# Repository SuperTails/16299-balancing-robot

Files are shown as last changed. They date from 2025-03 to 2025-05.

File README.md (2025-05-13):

# 16299 Balancing Robot PCB

Updated version of the PCB for 16299.

A submodule is used for some parts, so be sure to clone recursively:
```bash
git clone --recursive https://github.com/SuperTails/16299-balancing-robot.git
```

## Ordering PCBs

### 1 - Generate Bill of Materials

To generate the BoM:

1. Open the schematic editor
2. Open the "edit symbol fields" menu (table icon along the top ribbon)
3. Ensure the settings are as shown below
4. Hit "export".

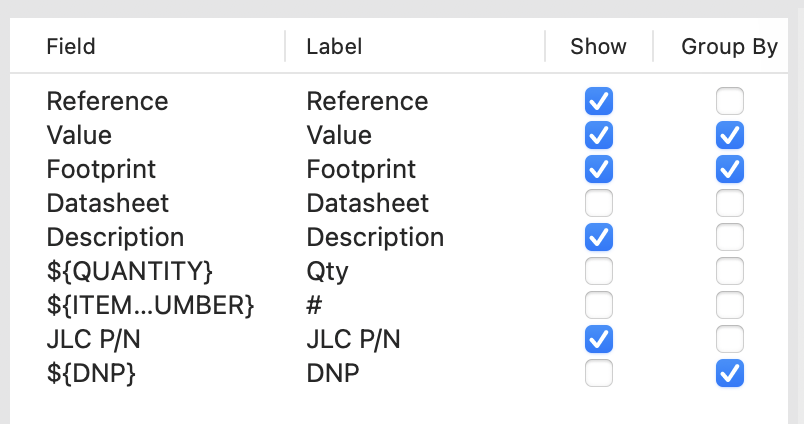
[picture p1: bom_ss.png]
BOM settings


### 2 - Generate Gerber Files

To generate the gerber files:
1. Open the PCB editor
2. File > Fabrication Outputs > Gerbers (.gbr)...
3. Ensure the settings are as shown below, including...
4. ... Make sure you set your output folder to `fab/`.
5. Click "Plot"

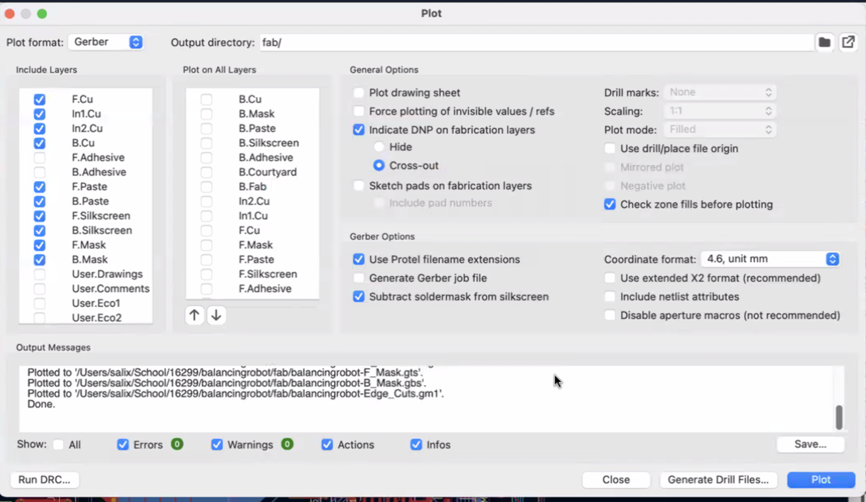
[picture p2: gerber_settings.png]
Gerber settings


More information for plotting Gerber and Drill files is available on
[JLC's guide](https://jlcpcb.com/help/article/how-to-generate-gerber-and-drill-files-in-kicad-7).

### 3 - Generate Drill Files

To generate the drill files:
1. From the Gerbers menu in the previous step, click "Generate Drill Files"
3. Ensure the settings are as shown below
5. Click "Generate"

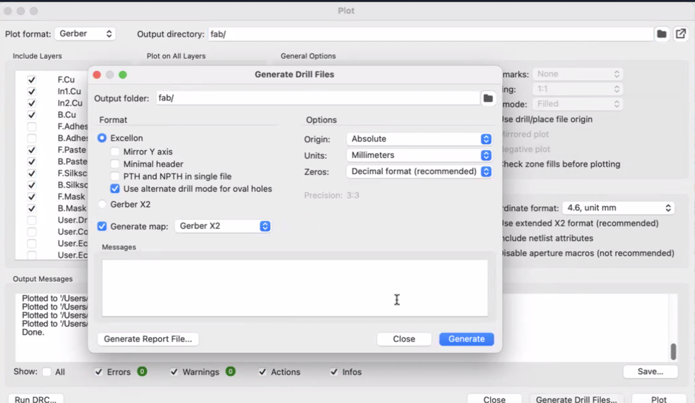
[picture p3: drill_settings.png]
Drill settings


More information for plotting Gerber and Drill files is available on
[JLC's guide](https://jlcpcb.com/help/article/how-to-generate-gerber-and-drill-files-in-kicad-7).

### 4 - Generate Placement Files

To generate the placement files:
1. Open the PCB editor
2. File > Fabrication Outputs > Component Placement (.pos, .gbr)...
3. Ensure the settings are as shown below
4. Click "Generate Position File"

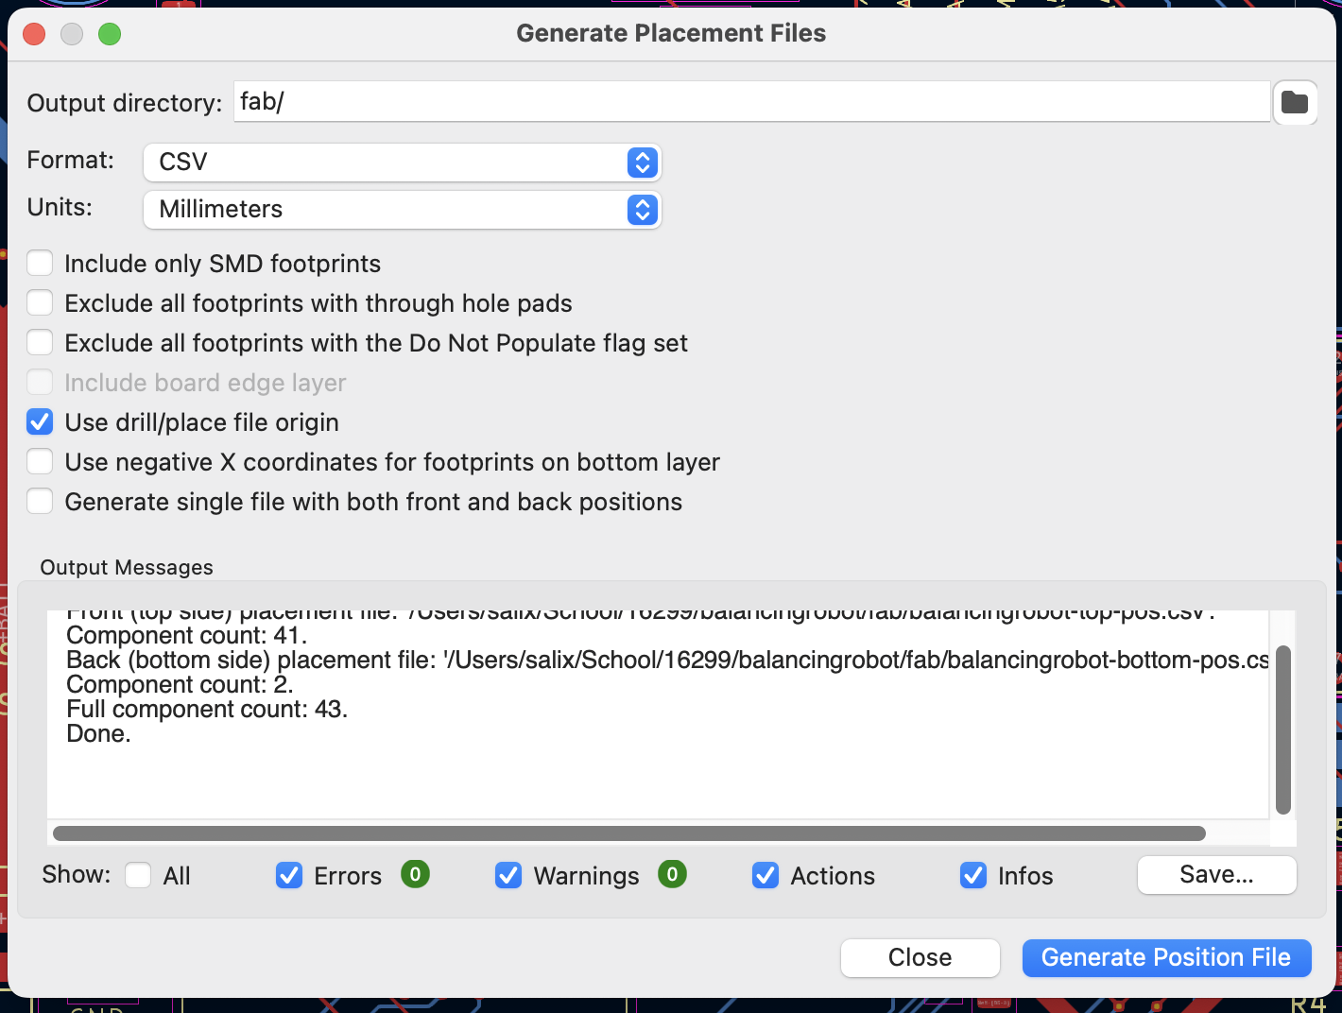
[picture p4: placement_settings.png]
Placement settings


### 5 - File Format Conversion

To convert the files into JLC's preferred format, run the `format_bom.py` script:

```bash
python3 format_bom.py
```

This will generate `fab/bom-jlc.csv` and `fab/balancingrobot-top-pos-jlc.csv`,
which should be used for JLC's PCB assembly options (discussed later).

### 6 - Upload Gerbers

Zip the `fab/` directory and upload it to [JLC's website](https://jlcpcb.com/).
Rarely, the file upload can take up to 10 minutes to complete.

### 7 - Select Ordering Options

Most settings should default correctly,
but there are a few changes:

1. Set the quantity to the desired amount
2. Ensure that the order mark is set to "Order Number (Specify Position)"
3. Enable "PCB Assembly"
4. Hit "next"

Quantity settings
Order settings
PCBA settings

### 8 - Uploading BOM and Placing Components

When prompted to "Upload BOM" and "Add CPL file",
upload `fab/bom-jlc.csv` and `fab/balancingrobot-top-pos-jlc.csv`.

It may issue a warning that D9 and D10 are not present in the CPL,
this is normal and you can continue.
D9 and D10 are the IR LEDs which are mounted on the underside of the board,
and doing assembly for both top and bottom components makes shipping difficult.

All parts should be selected in the right column and there should be no other errors.

When moving on to placement, JLC may note that
"The system detects component that may be offset from the PCB,
does it try to automatically align it?"
Click **cancel** on this prompt, as it will displace many of the components to the wrong place.

The through-hole components typically need to be both rotated and dragged to fit;
the surface mount components should **only be rotated**.

Ensure that all surface mount components
**have the pink dot (pin 1) aligned with the corresponding silkscreen arrow**.
Some of the SMD components may be upside-down.

There will be four rows of header pins far above the rest of the PCB (shown below);
these are the sockets for the Arduino Nano and the motor driver.
Be sure to place them as well.

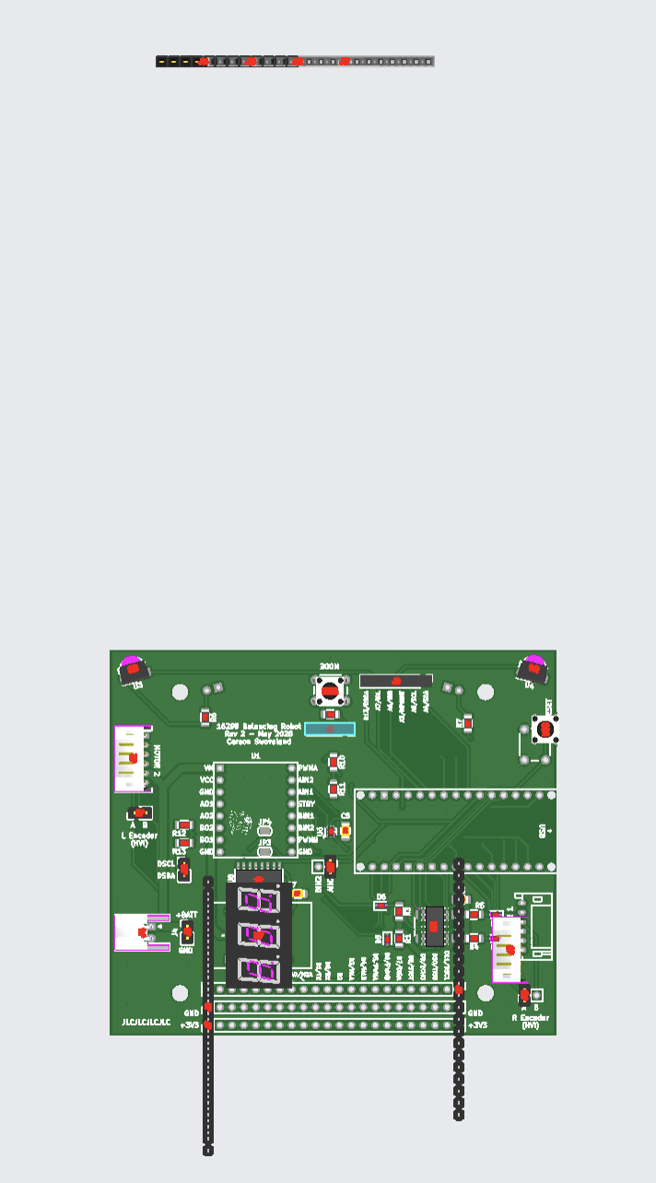
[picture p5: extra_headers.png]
Displaced headers


Once placement is finished, the board should appear as shown below:

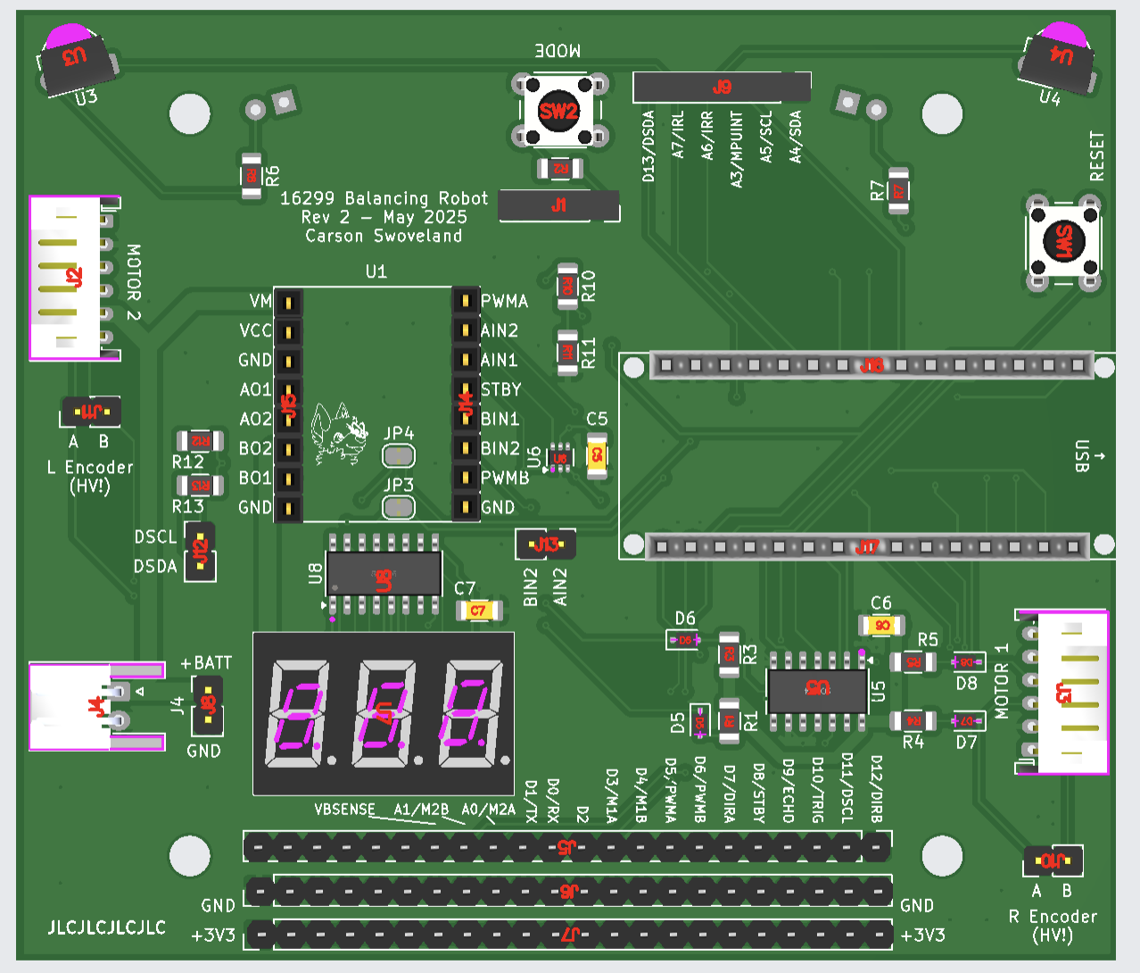
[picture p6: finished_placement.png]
Finished placement


When prompted to select a category for your order, I usually select "Robot",
as shown below:

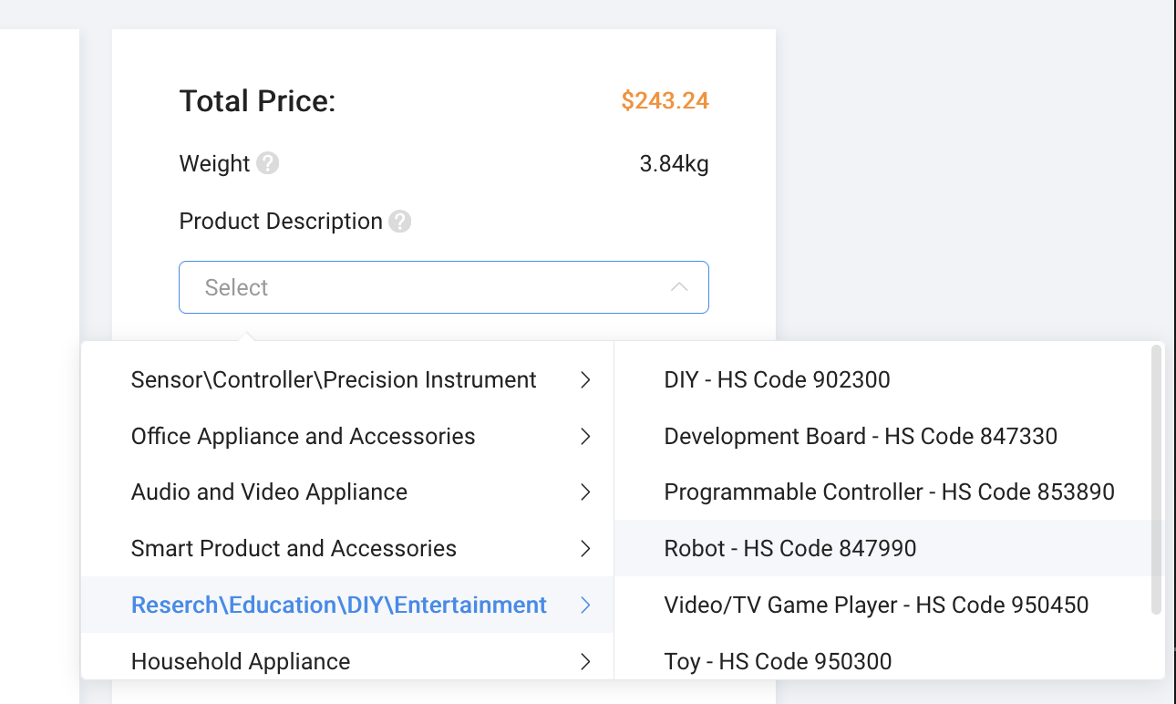
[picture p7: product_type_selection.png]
Product type selection


This completes all the placement steps,
simply complete the rest of the checkout steps to order the PCB.

**After ordering, you may receive an email saying that the footprint of the 7-segment display is incorrect.**
**As long as the decimal point is on the bottom and the pink dot is in the bottom left, reply to the email and say the placement is correct.**

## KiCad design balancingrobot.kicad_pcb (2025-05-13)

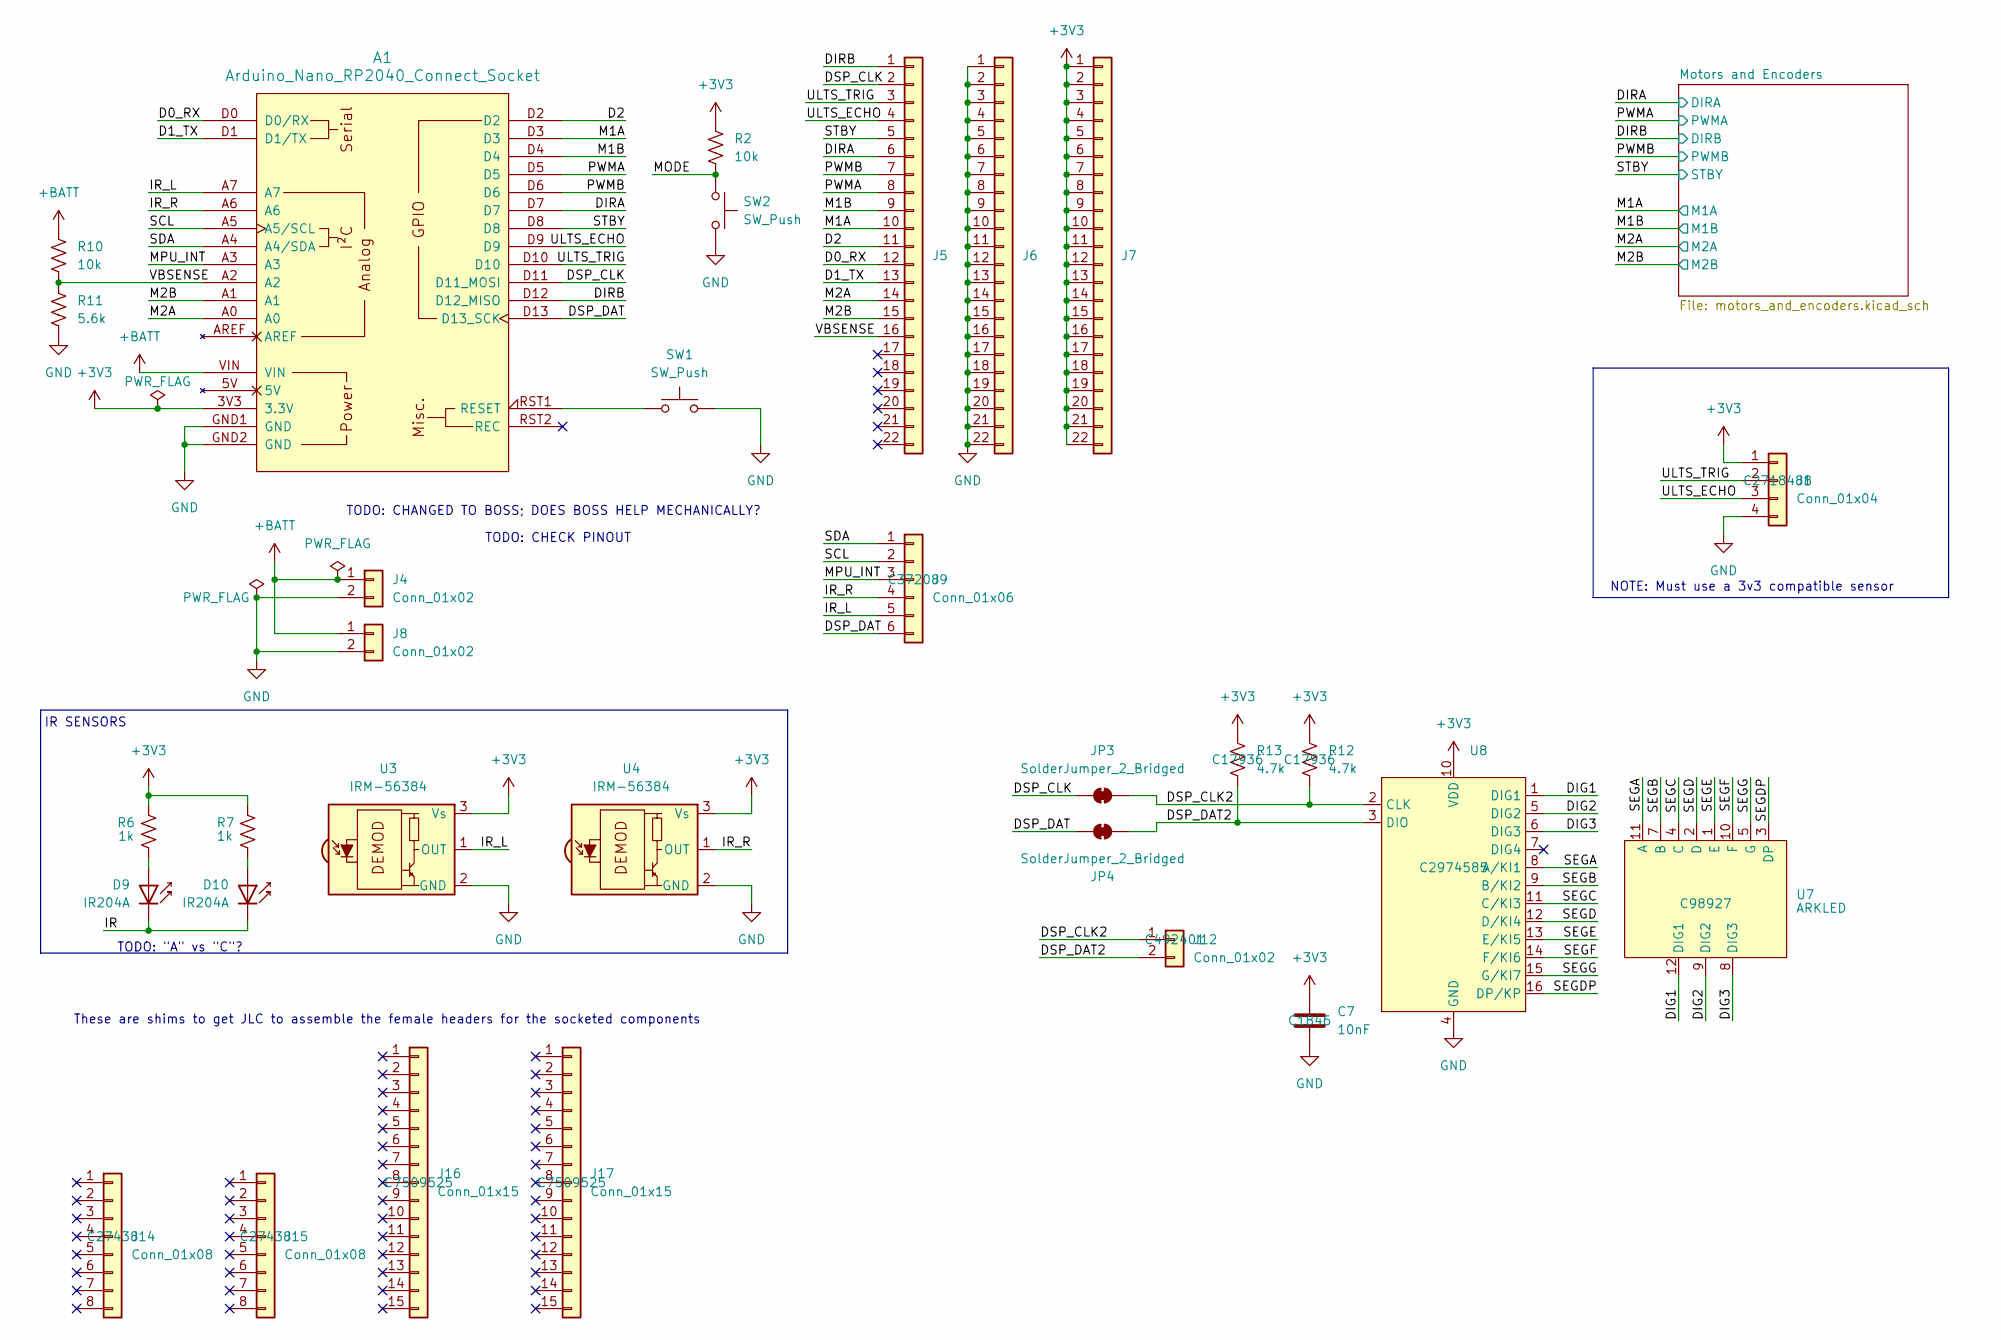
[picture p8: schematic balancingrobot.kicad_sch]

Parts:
A1: Arduino_Nano_RP2040_Connect_Socket; Arduino_Nano_Every_Socket
C7: 10nF; C_1206_3216Metric; JLC P/N C1846
D9, D10: IR204A; LED_D3.0mm_IRBlack; JLC P/N C2936547
J1: Conn_01x04; PinSocket_1x04_P2.54mm_Vertical; JLC P/N C2718488
J4: Conn_01x02; JST_XH_S2B-XH-A-1_1x02_P2.50mm_Horizontal; JLC P/N C163035
J5, J6, J7: Conn_01x22; PinHeader_1x22_P2.54mm_Vertical; JLC P/N C725954
J8, J12: Conn_01x02; PinHeader_1x02_P2.54mm_Vertical; JLC P/N C492401
J9: Conn_01x06; PinHeader_1x06_P2.54mm_Vertical; JLC P/N C37208
J14, J15: Conn_01x08; PinSocket_1x08_P2.54mm_Vertical; JLC P/N C27438
J16, J17: Conn_01x15; PinSocket_1x15_P2.54mm_Vertical; JLC P/N C7509525
JP3, JP4: SolderJumper_2_Bridged; SolderJumper-2_P1.3mm_Bridged_RoundedPad1.0x1.5mm
R2, R10: 10k; R_1206_3216Metric; JLC P/N C17902
R6, R7: 1k; R_1206_3216Metric; JLC P/N C4410
R11: 5.6k; R_1206_3216Metric; JLC P/N C18028
R12, R13: 4.7k; R_1206_3216Metric; JLC P/N C17936
SW1, SW2: SW_Push; SW_PUSH_6mm; JLC P/N C255811
U3, U4: IRM-56384; Vishay_MOLD-3Pin; JLC P/N C72048
U7: ARKLED; ARKLED(Wuxi ARK Tech Elec) SP420361N; JLC P/N C98927
U8: SOP-16_3.9x9.9mm_P1.27mm; JLC P/N C2974585

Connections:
+3V3: A1.3V3 (3.3V), C7.1, J1.1, J7.1, J7.2, J7.3, J7.4, J7.5, J7.6, J7.7, J7.8, J7.9, J7.10, J7.11, J7.12, J7.13, J7.14, J7.15, J7.16, J7.17, J7.18, J7.19, J7.20, J7.21, J7.22, R2.1, R6.2, R7.1, R12.1, R13.1, U3.3 (Vs), U4.3 (Vs), U8.10 (VDD); also elsewhere on the board
+BATT: A1.VIN, J4.1, J8.1, R10.1; also elsewhere on the board
/D0_RX: A1.D0 (D0/RX), J5.12
/D1_TX: A1.D1 (D1/TX), J5.13
/D2: A1.D2, J5.11
/DIG1: U7.12 (DIG1), U8.1 (DIG1)
/DIG2: U7.9 (DIG2), U8.5 (DIG2)
/DIG3: U7.8 (DIG3), U8.6 (DIG3)
/DIRA: A1.D7, J5.6; also elsewhere on the board
/DIRB: A1.D12 (D12_MISO), J5.1; also elsewhere on the board
/DSP_CLK: A1.D11 (D11_MOSI), J5.2, JP3.1 (A)
/DSP_CLK2: J12.1, JP3.2 (B), R12.2, U8.2 (CLK)
/DSP_DAT: A1.D13 (D13_SCK), J9.6, JP4.1 (A)
/DSP_DAT2: J12.2, JP4.2 (B), R13.2, U8.3 (DIO)
/IR: D9.1 (K), D10.1 (K)
/IR_L: A1.A7, J9.5, U3.1 (OUT)
/IR_R: A1.A6, J9.4, U4.1 (OUT)
/M1A: A1.D3, J5.10; also elsewhere on the board
/M1B: A1.D4, J5.9; also elsewhere on the board
/M2A: A1.A0, J5.14; also elsewhere on the board
/M2B: A1.A1, J5.15; also elsewhere on the board
/MODE: R2.2, SW2.1
/MPU_INT: A1.A3, J9.3
/PWMA: A1.D5, J5.8; also elsewhere on the board
/PWMB: A1.D6, J5.7; also elsewhere on the board
/SCL: A1.A5 (A5/SCL), J9.2
/SDA: A1.A4 (A4/SDA), J9.1
/SEGA: U7.11 (A), U8.8 (A/KI1)
/SEGB: U7.7 (B), U8.9 (B/KI2)
/SEGC: U7.4 (C), U8.11 (C/KI3)
/SEGD: U7.2 (D), U8.12 (D/KI4)
/SEGDP: U7.3 (DP), U8.16 (DP/KP)
/SEGE: U7.1 (E), U8.13 (E/KI5)
/SEGF: U7.10 (F), U8.14 (F/KI6)
/SEGG: U7.5 (G), U8.15 (G/KI7)
/STBY: A1.D8, J5.5; also elsewhere on the board
/ULTS_ECHO: A1.D9, J1.3, J5.4
/ULTS_TRIG: A1.D10, J1.2, J5.3
/VBSENSE: A1.A2, J5.16, R10.2, R11.1
GND: A1.GND1 (GND), A1.GND2 (GND), C7.2, J1.4, J4.2, J6.1, J6.2, J6.3, J6.4, J6.5, J6.6, J6.7, J6.8, J6.9, J6.10, J6.11, J6.12, J6.13, J6.14, J6.15, J6.16, J6.17, J6.18, J6.19, J6.20, J6.21, J6.22, J8.2, R11.2, SW1.2, SW2.2, U3.2 (GND), U4.2 (GND), U8.4 (GND); also elsewhere on the board
unnamed: A1.RST1 (RESET), SW1.1
unnamed: D9.2 (A), R6.1
unnamed: D10.2 (A), R7.2

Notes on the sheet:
IR SENSORS
TODO: "A" vs "C"?
These are shims to get JLC to assemble the female headers for the socketed components
NOTE: Must use a 3v3 compatible sensor
TODO: CHECK PINOUT
TODO: CHANGED TO BOSS; DOES BOSS HELP MECHANICALLY?

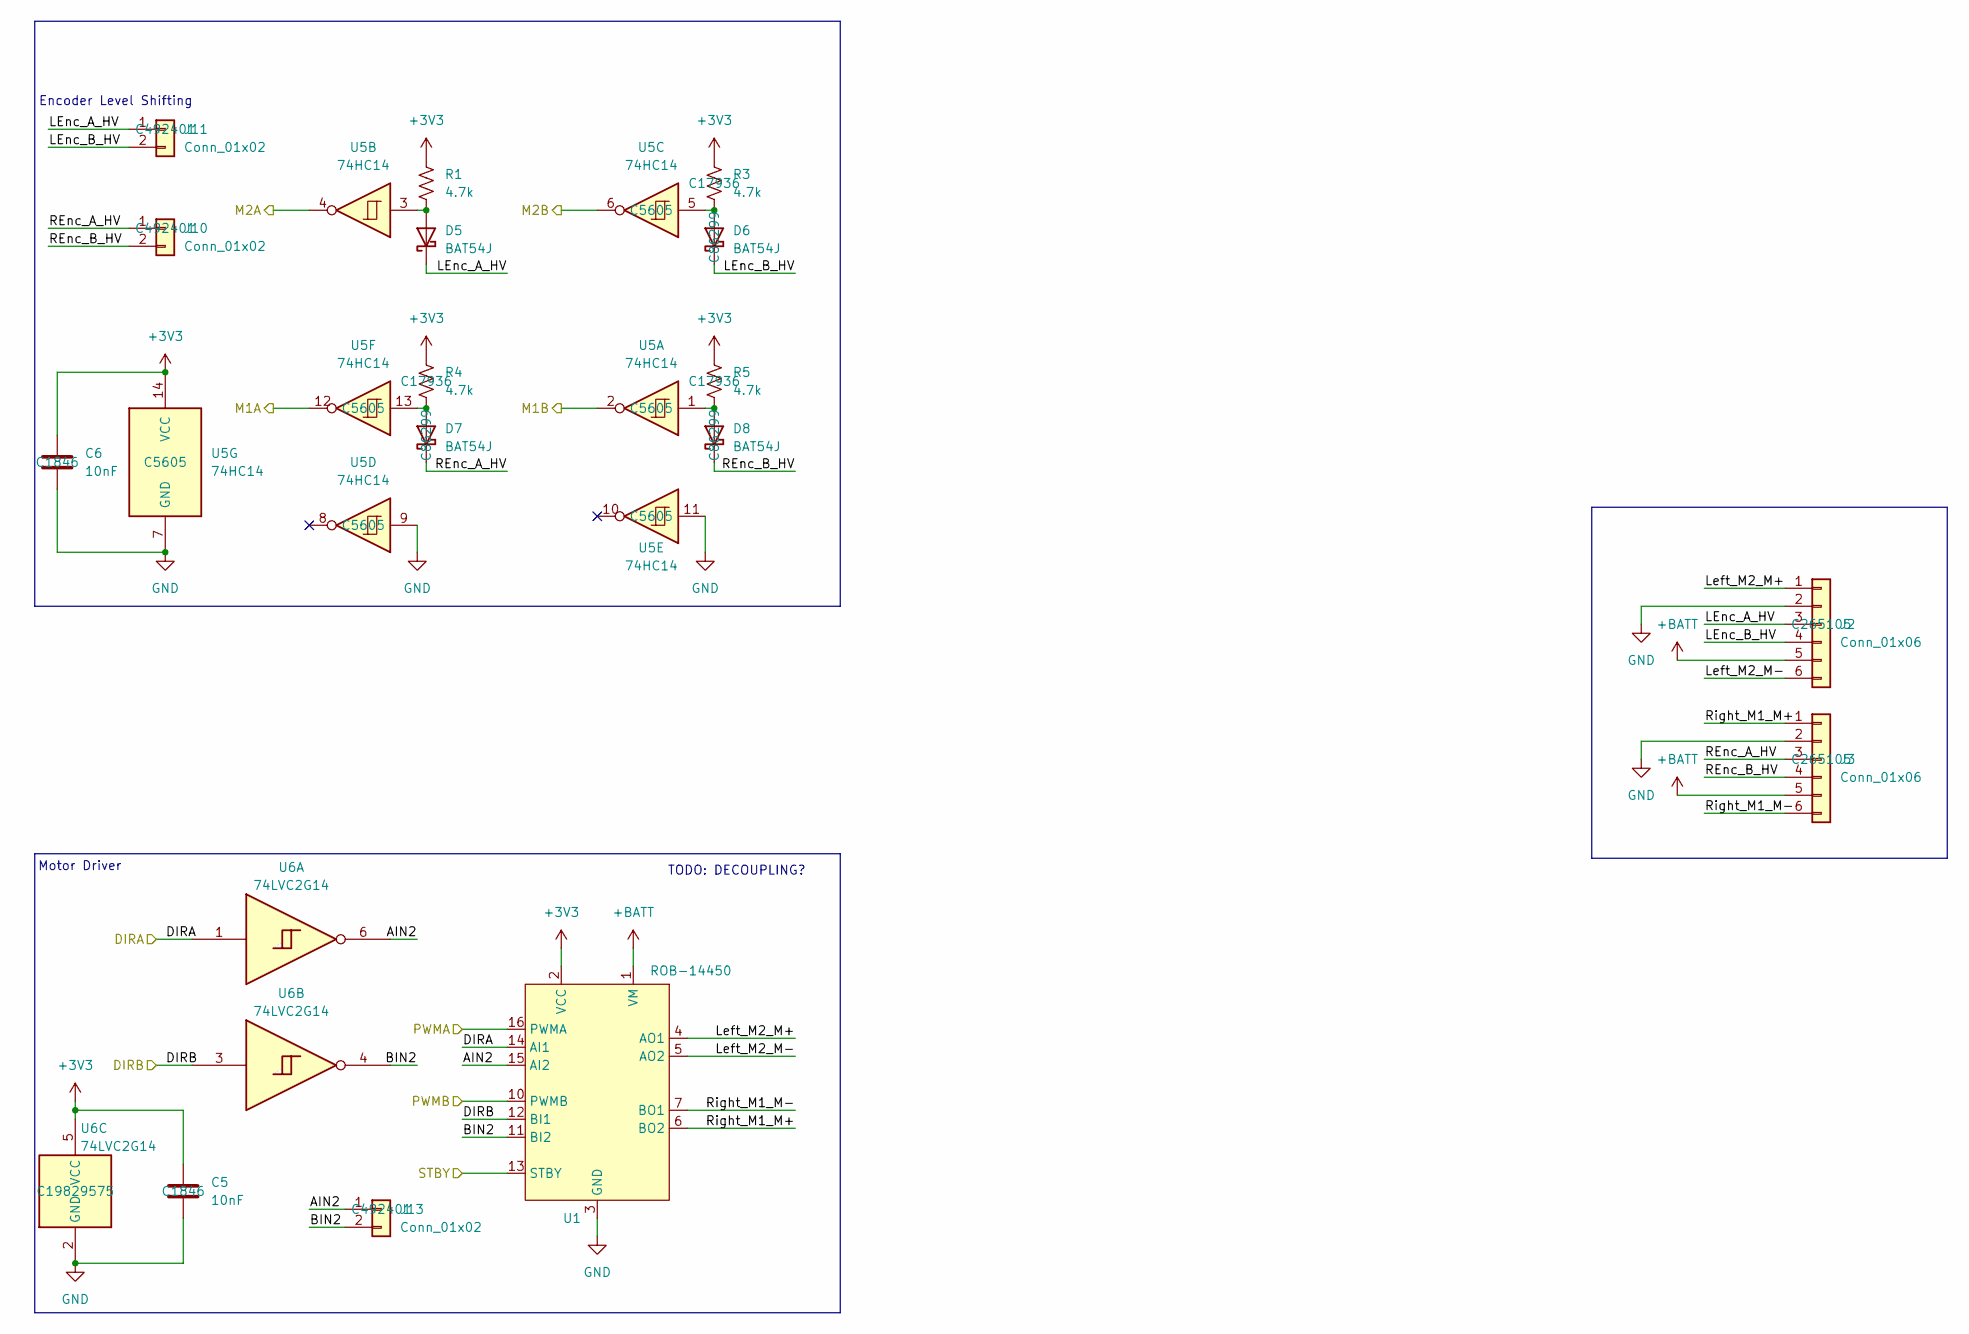
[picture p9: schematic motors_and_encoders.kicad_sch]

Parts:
C5, C6: 10nF; C_1206_3216Metric; JLC P/N C1846
D5, D6, D7, D8: BAT54J; D_SOD-323F; JLC P/N C86299
J2, J3: Conn_01x06; JST_PH_S6B-PH-K_1x06_P2.00mm_Horizontal; JLC P/N C265105
J10, J11, J13: Conn_01x02; PinHeader_1x02_P2.54mm_Vertical; JLC P/N C492401
R1, R3, R4, R5: 4.7k; R_1206_3216Metric; JLC P/N C17936
U1: ROB-14450; ROB-14451
U5: 74HC14; SOIC-14_3.9x8.7mm_P1.27mm; JLC P/N C5605
U6: 74LVC2G14; SOT-363_SC-70-6; JLC P/N C19829575

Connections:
+3V3: C5.1, C6.1, R1.2, R3.2, R4.2, R5.2, U1.2 (VCC), U5.14 (VCC), U6.5 (VCC); also elsewhere on the board
+BATT: J2.5, J3.5, U1.1 (VM); also elsewhere on the board
/DIRA: U1.14 (AI1), U6.1; also elsewhere on the board
/DIRB: U1.12 (BI1), U6.3; also elsewhere on the board
/M1A: U5.12; also elsewhere on the board
/M1B: U5.2; also elsewhere on the board
/M2A: U5.4; also elsewhere on the board
/M2B: U5.6; also elsewhere on the board
/Motors and Encoders/AIN2: J13.1, U1.15 (AI2), U6.6
/Motors and Encoders/BIN2: J13.2, U1.11 (BI2), U6.4
/Motors and Encoders/LEnc_A_HV: D5.1 (K), J2.3, J11.1
/Motors and Encoders/LEnc_B_HV: D6.1 (K), J2.4, J11.2
/Motors and Encoders/Left_M2_M+: J2.1, U1.4 (AO1)
/Motors and Encoders/Left_M2_M-: J2.6, U1.5 (AO2)
/Motors and Encoders/REnc_A_HV: D7.1 (K), J3.3, J10.1
/Motors and Encoders/REnc_B_HV: D8.1 (K), J3.4, J10.2
/Motors and Encoders/Right_M1_M+: J3.1, U1.6 (BO2)
/Motors and Encoders/Right_M1_M-: J3.6, U1.7 (BO1)
/PWMA: U1.16 (PWMA); also elsewhere on the board
/PWMB: U1.10 (PWMB); also elsewhere on the board
/STBY: U1.13 (STBY); also elsewhere on the board
GND: C5.2, C6.2, J2.2, J3.2, U1.3 (GND), U1.8 (GND), U1.9 (GND), U5.7 (GND), U5.9, U5.11, U6.2 (GND); also elsewhere on the board
unnamed: D5.2 (A), R1.1, U5.3
unnamed: D6.2 (A), R3.1, U5.5
unnamed: D7.2 (A), R4.1, U5.13
unnamed: D8.2 (A), R5.1, U5.1

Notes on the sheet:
Encoder Level Shifting
TODO: DECOUPLING?
Motor Driver

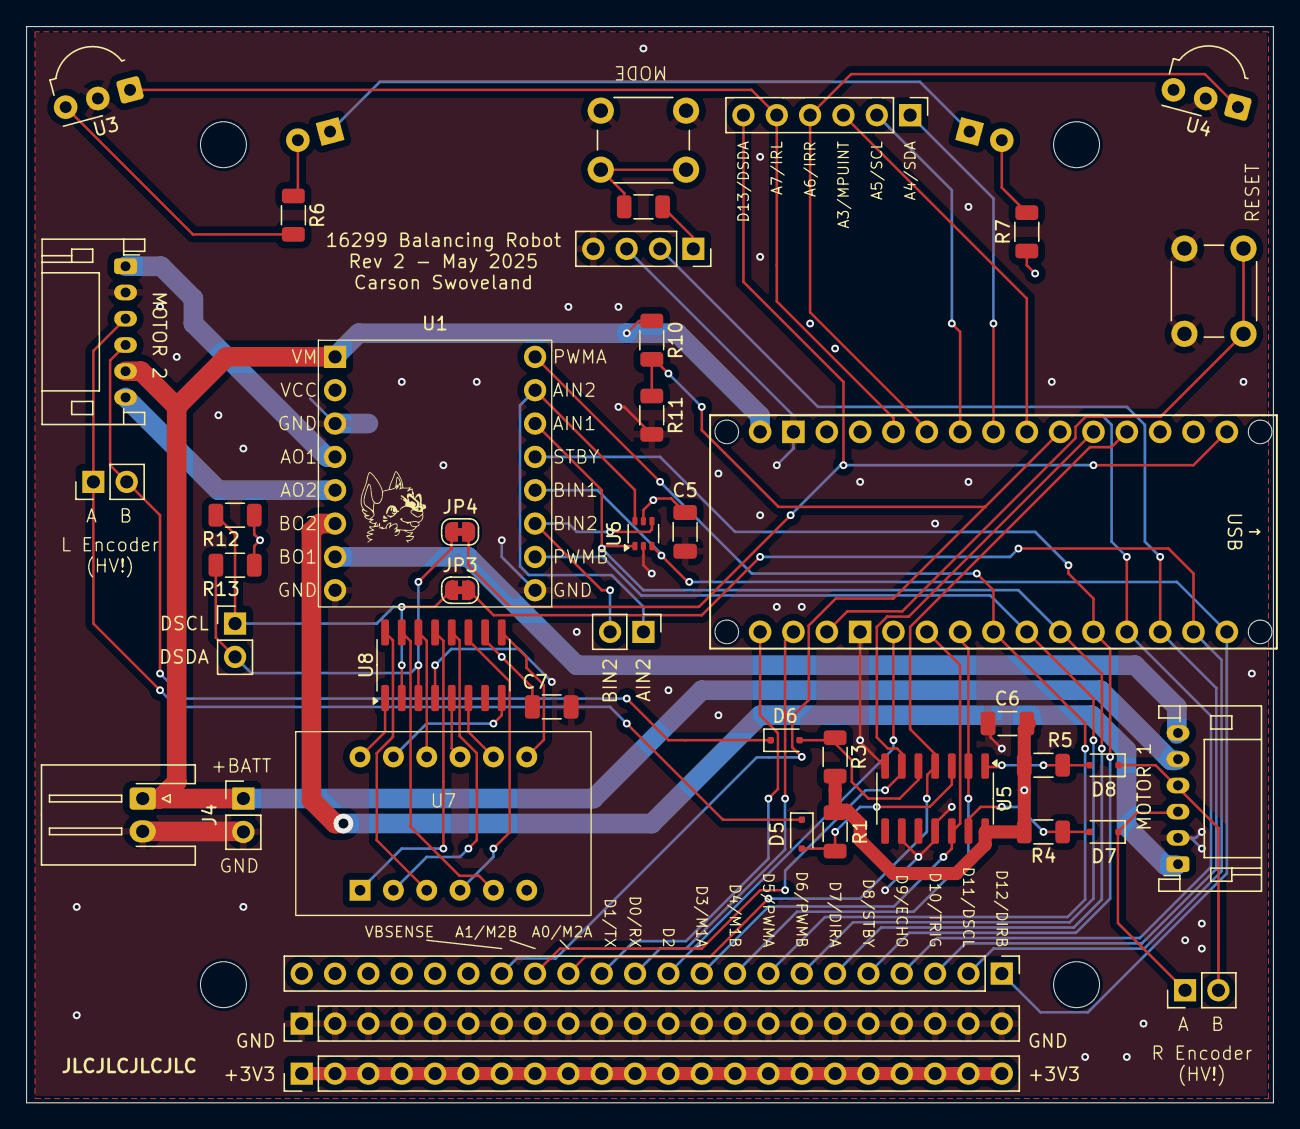
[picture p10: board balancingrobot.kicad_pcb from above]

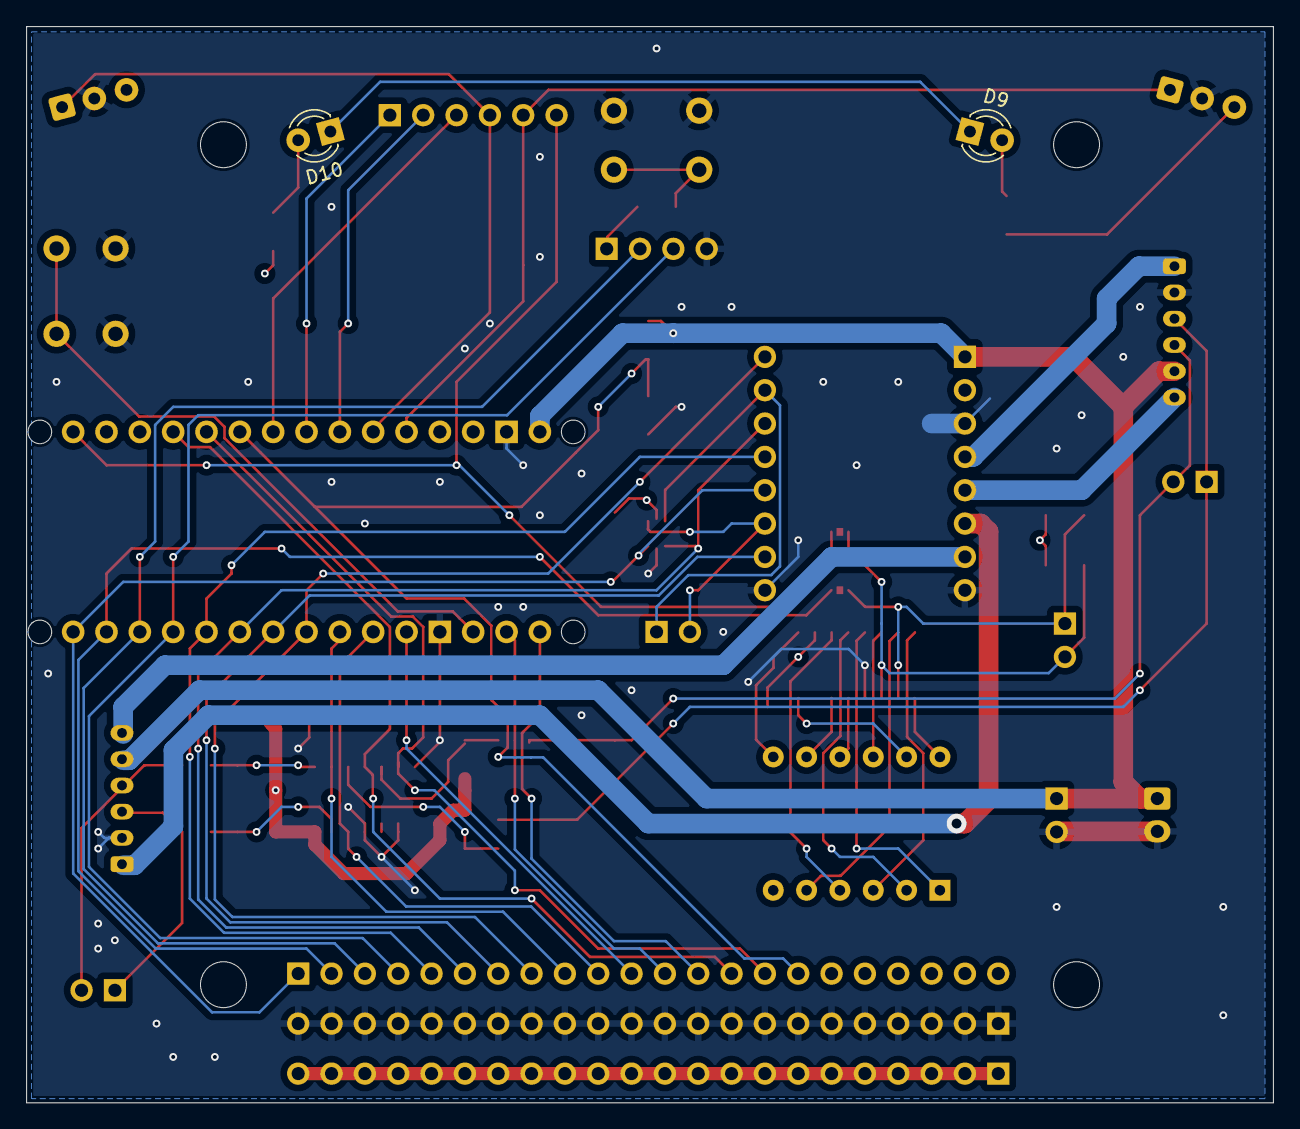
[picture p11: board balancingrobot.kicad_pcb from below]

Board: 4 copper layers, 95.0 x 82.0 mm, 45 parts (2 on the bottom side), 57 nets.

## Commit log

2025-03-24 Update silkscreen and change to 4 layer
    [balancingrobot.kicad_pcb]
2025-03-26 Remove MPU6050
    [balancingrobot.kicad_pcb, balancingrobot.kicad_sch]
